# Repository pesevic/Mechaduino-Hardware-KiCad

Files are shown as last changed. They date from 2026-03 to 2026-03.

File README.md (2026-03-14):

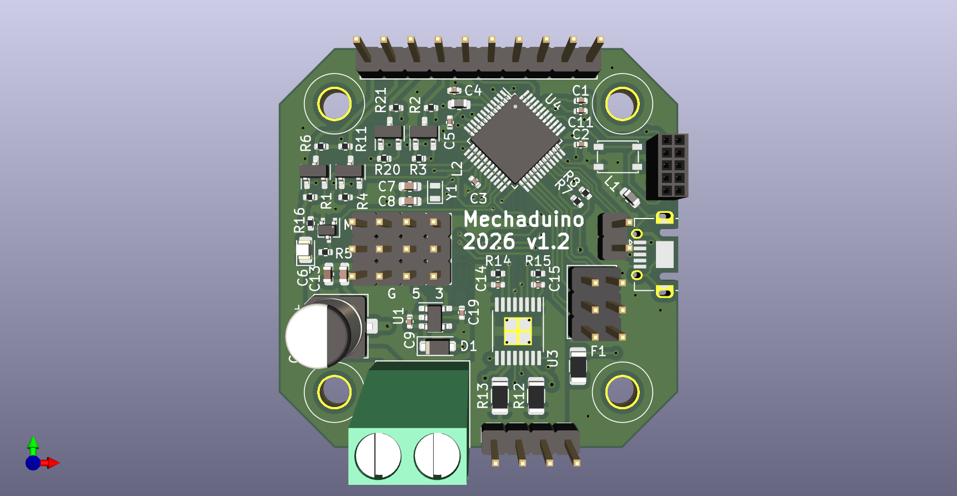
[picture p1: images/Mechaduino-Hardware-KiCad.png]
3D Render of Mechaduino PCB

# Overview
This repository contains an updated KiCad port of [jcchurch13's](https://github.com/jcchurch13/Mechaduino-Hardware) Mechaduino hardware. 

As a part of my master's thesis, I wanted to revive the Mechaduino-based [TorqueTuner](https://github.com/IDMIL/TorqueTuner), a rotary haptic device developed at the Input Devices and Music Interaction Laboratory (IDMIL) at McGill University. Since the Mechaduino has been out of production for some years, and because the original design files are in EAGLE (a now-defunct, proprietary software), I have ported the schematics and board layout to KiCad, a free and open-source (and incredibly powerful) PCB design software. 

While retaining the original circuit design, I have updated the schematics and created a new PCB layout from scratch, using KiCad's built-in component libraries. I have also included PCB fabrication/assembly files (.gbr, .drl, BOM, CPL). Most importantly, since the design is now more readily accessible, I hope it will be much easier to adapt and redesign the hardware for various stepper motors and applications.

Below, I have included some useful information if you wish to adopt or adapt the Mechaduino for your own project.

# Guide
This section serves as a guide for manufacturing and programming the Mechaduino.
## Mechaduino Summary
The [Mechaduino](https://github.com/jcchurch13/Mechaduino-Hardware) is an open-source stepper motor servo designed by [Tropical Labs](https://tropical-labs.com/mechaduino/). Its relatively small size and affordability make it attractive for mechatronics applications.

Integrated circuits on the board include a motor driver (A4954), magnetic encoder (AS5047D), 3.3 V linear voltage regulator (TLV70233), and an Arduino Zero-compatible microcontroller (ATSAMD21G18A-A). It can be powered via USB or an external 5 V source. The motor is powered through a terminal block, accepting a supply voltage between 8 V and 35 V. A range of Arduino I/O pins are accessible through the header pins, including those for I2C and SPI communication. See the schematic for more detail.

The board is designed to fit onto the back of a NEMA 17 motor.

## PCB Manufacturing
If you wish to obtain Mechaduino PCBs for yourself, you may follow what I suggest below, which is how I ordered them for myself.

For manufacturing and assembly, I used [jlcpcb.com](jlcpcb.com). Upload the zipped fabrication files to JLC, and add the PCB assembly option. Since two-layer boards can only be assembled on one side, choose the top side. The magnetic encoder and its decoupling capacitor can be soldered manually later. Upload the corresponding bill of materials and component position list .csv files. **Note that you may need to select alternative parts or reposition components in the board preview.** I have had to flip C12 and align J9 (USB connector) each time I've processed the PCBs.

## Device Assembly
Besides the Mechaduino PCB, you will need the following parts (the links direct to the parts I used):
 - [a NEMA 17 stepper motor](https://www.omc-stepperonline.com/nema-17-bipolar-45ncm-64oz-in-2a-42x42x40mm-4-wires-w-1m-cable-connector-17hs16-2004s1),
 - [a diametrically magnetized NdFeB magnet](https://www.digikey.ca/en/products/detail/radial-magnets-inc/8996/5126078),
 - an AS5074D magnetic encoder IC,
 - an 0.1 uF 0805 SMD capacitor,
 - 2.54 mm pitch header pins,
 - long M3 screws/threaded rods,
 - standoffs of some sort (I used washers), and
 - super glue.

Follow these steps (based on instructions in [Tropical Labs' manual](https://tropical-labs.com/wp-content/uploads/2018/11/Mechaduino-Manual-0.1.3.pdf)):
1. Solder the encoder and capacitor to the back of the PCB with an iron/reflow/oven. Also add the header pins.
2. Super glue the magnet onto the back of the motor shaft. Center it as much as possible.
3. Mount the PCB to the motor using the threaded rods and standoffs. The PCB should sit a couple of milimeters away from the motor.

Your Mechaduino should now be ready to be programmed.

## Programming
Flashing an Arduino Zero bootloader onto the custom MCU circuit was, for me, the most challenging part of this build. I used an ST-LINK V2 USB programmer paired with [Adafruit Adalink](https://github.com/adafruit/Adafruit_Adalink) to upload the bootloader via the PCB's SWD pins. This may be easier on Mac, but I can only speak for the Herculean procedure required for Windows users. Besides the USB programmer, you will need some way of connecting the programmer to the pins. I used an SWD breakout board connected to the programmer with jumper wires.

Follow the installation instructions on the [Adalink repository](https://github.com/adafruit/Adafruit_Adalink). Note, however, that I could not get Adalink to work with any version of Python newer than 2.7.13 (this was using Adalink 2.2.0 and OpenOCD 0.12.0). You may need to downgrade Python to an older version.

Once you have confirmed that Adalink is working in CMD, clone the [ArduinoCore-samd repository](https://github.com/arduino/arduinocore-samd) to get the bootloader. CD into `/ArduinoCore-samd/bootloaders/zero`. Wipe the board and flash the bootloader with the following two commands:
```
adalink atsamd21g18 -p stlink -w
adalink -v atsamd21g18 -p stlink -h samd21_sam_ba.hex
```
Check whether the 5888 bytes are verified. If not, unplugging and plugging the ST-LINK USB dongle into my computer seemed to fix things. Once the MCU has successfully been flashed, connect the Mechaduino to your computer via the micro-USB port. Double-pressing the reset button on the PCB should make the device appear as an Arduino Zero in Device Manager or in the Arduino IDE.

Finally, clone the [Mechaduino Firmware](https://github.com/jcchurch13/Mechaduino-Firmware) repository and upload the code to the board via the Arduino IDE. You should now have a fully functioning Mechaduino. Run the calibration routine and tests as described in [Tropical Labs' manual](https://tropical-labs.com/wp-content/uploads/2018/11/Mechaduino-Manual-0.1.3.pdf).

# License
This project is released under the [Creative Commons Attribution-ShareAlike 4.0](https://creativecommons.org/licenses/by-sa/4.0/) license, and is not endorsed by the original creator.

*No generative AI was used in any part of this project.*

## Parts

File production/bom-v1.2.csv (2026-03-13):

Designator | Footprint | Quantity | Value | LCSC Part #
C1, C14, C15, C16, C2, C3, C4, C5 | 402 | 8 | 0.1u | C169842
C11, C19, C9 | 402 | 3 | 1.0u | C29266
C12 | CP_Elec_6.3x7.7 | 1 | 100u | C178560
C13 | 603 | 1 | 1.0u | C5673
C6 | 603 | 1 | 0.01u | C1589
C7, C8 | 603 | 2 | 18p | C165734
D1 | D_SOD-123F | 1 | SMF5.0CA | C283867
F1 | 1206 | 1 | ASMD1206-050 | C883127
J1 | TerminalBlock_Phoenix_MKDS-1,5-2_1x02_P5.00mm_Horizontal | 1 | Screw_Terminal_01x02 | C3817933
J9 | USB_Micro-AB_Molex_47590-0001 | 1 | USB_B_Micro | C136001
L1, L2 | 603 | 2 | BLM18PG471SN1D | C97853
LED1 | 805 | 1 | Green | C2899888
Q1, Q2, Q3, Q4 | SOT-23-3 | 4 | BSS138 | C534601
Q5 | SOT-323_SC-70 | 1 | 2N7002 | C139444
R1, R11, R2, R20, R21, R3, R4, R6 | 402 | 8 | 10k | C71617
R12, R13 | 1206 | 2 | 0.15 | C37936
R14, R15 | 402 | 2 | 1k | C71623
R16 | 402 | 1 | 100k | C481918
R5 | 402 | 1 | 330 | C25104
R7, R8 | 402 | 2 | 4.7k | C482193
SW1 | SW_SPST_PTS810 | 1 | SW_SPST | C221896
U1 | SOT-23-5 | 1 | TLV70233_SOT23-5 | C110287
U2 | TSSOP-14_4.4x5mm_P0.65mm | 1 | AS5047D | C2693743
U3 | TSSOP-16-1EP_4.4x5mm_P0.65mm_EP3x3mm_ThermalVias | 1 | A4954 | C2688265
U4 | TQFP-48_7x7mm_P0.5mm | 1 | ATSAMD21G18A-A | C78624
Y1 | Crystal_SMD_2012-2Pin_2.0x1.2mm | 1 | 32.768k | C907552

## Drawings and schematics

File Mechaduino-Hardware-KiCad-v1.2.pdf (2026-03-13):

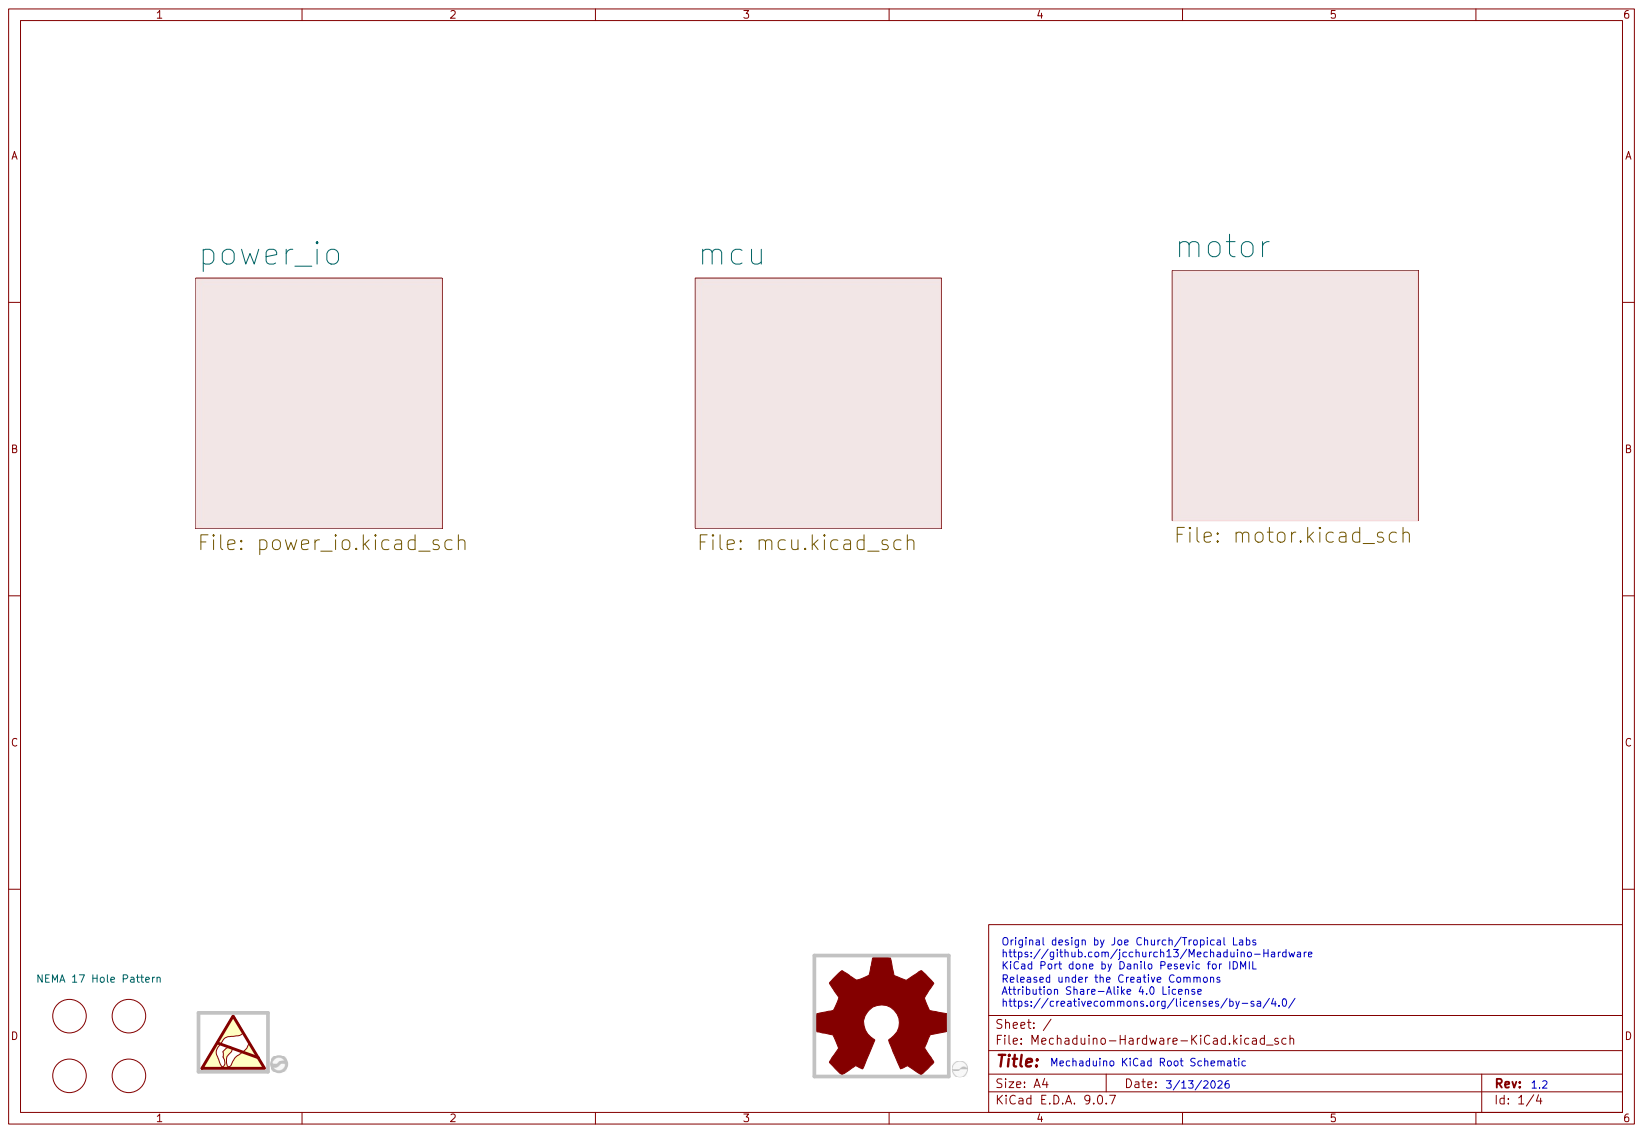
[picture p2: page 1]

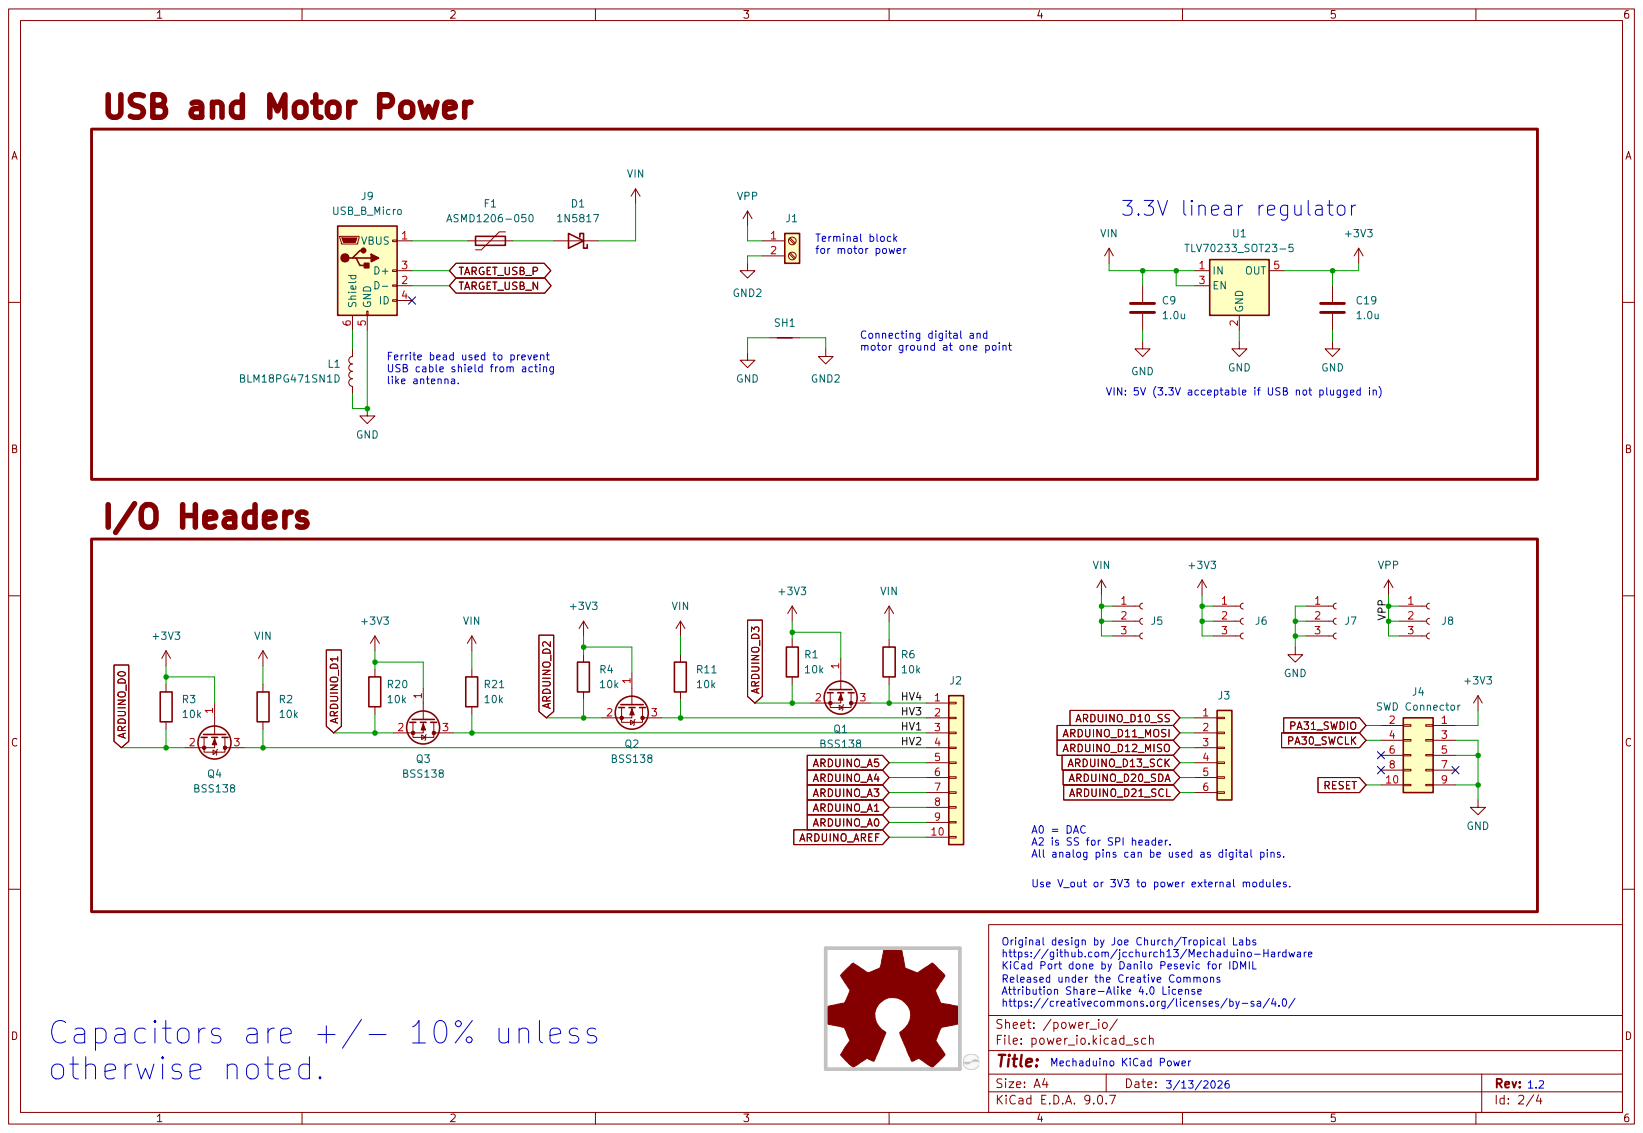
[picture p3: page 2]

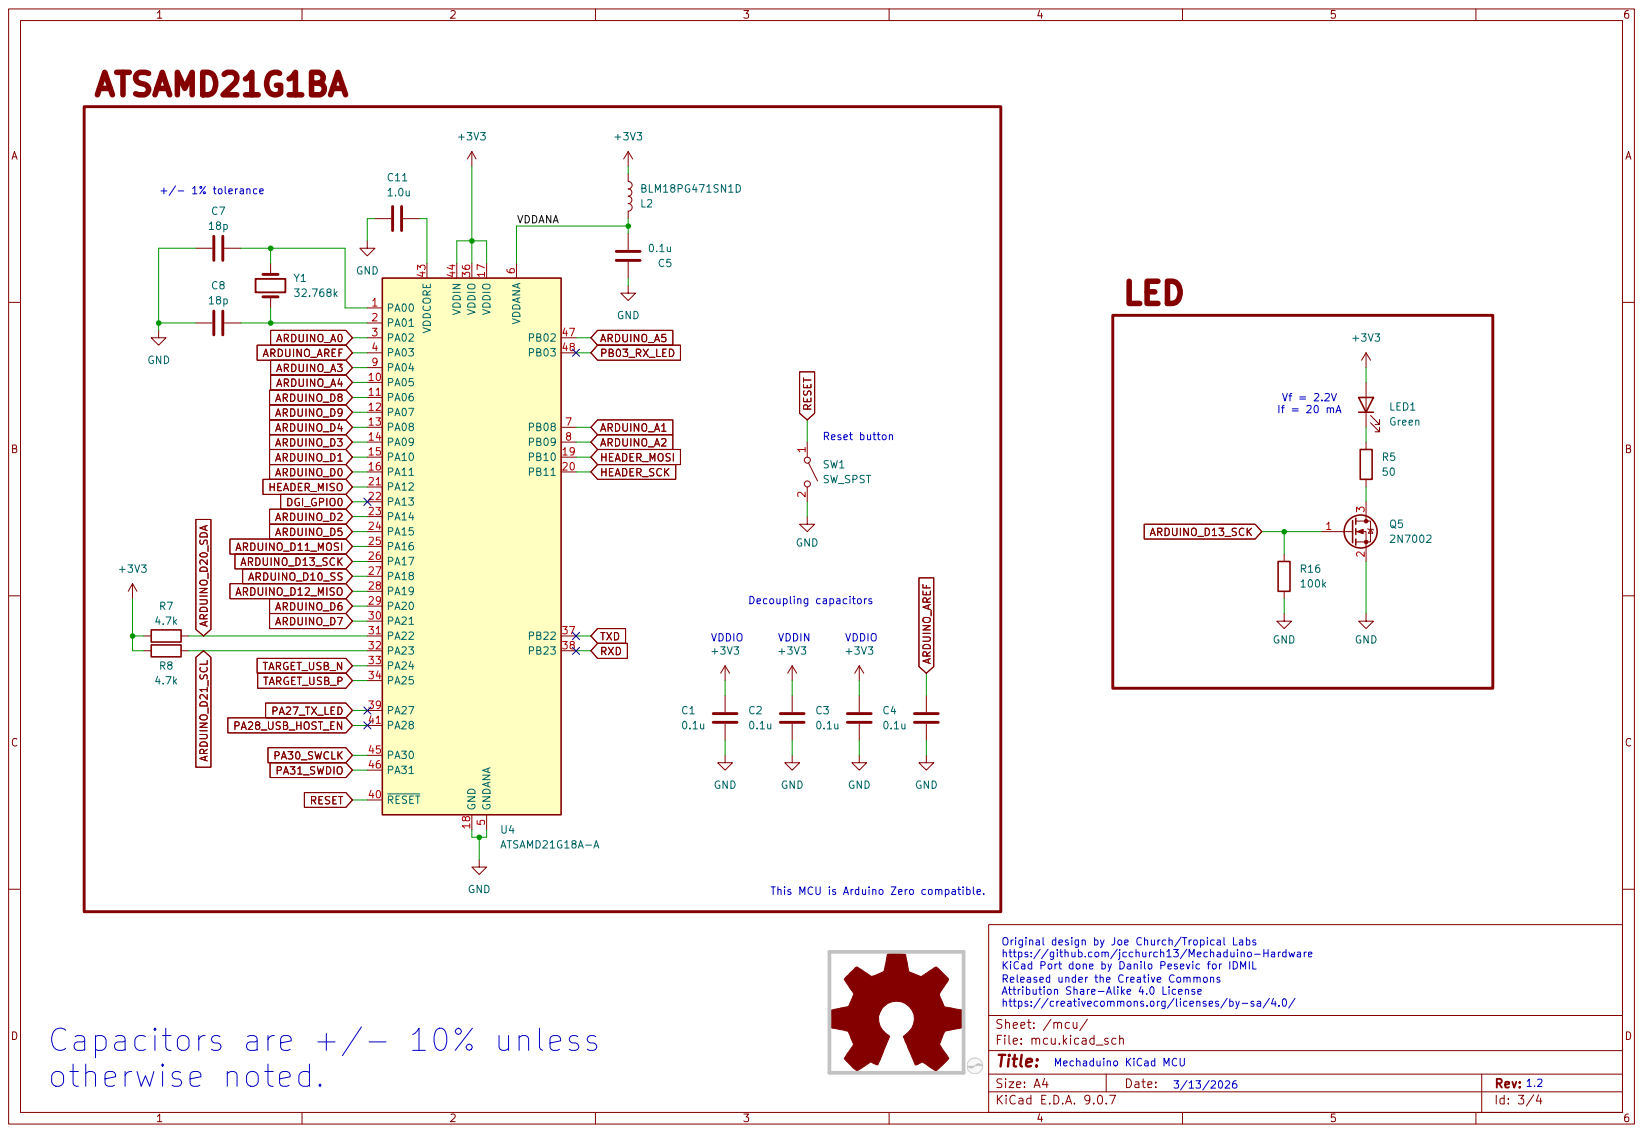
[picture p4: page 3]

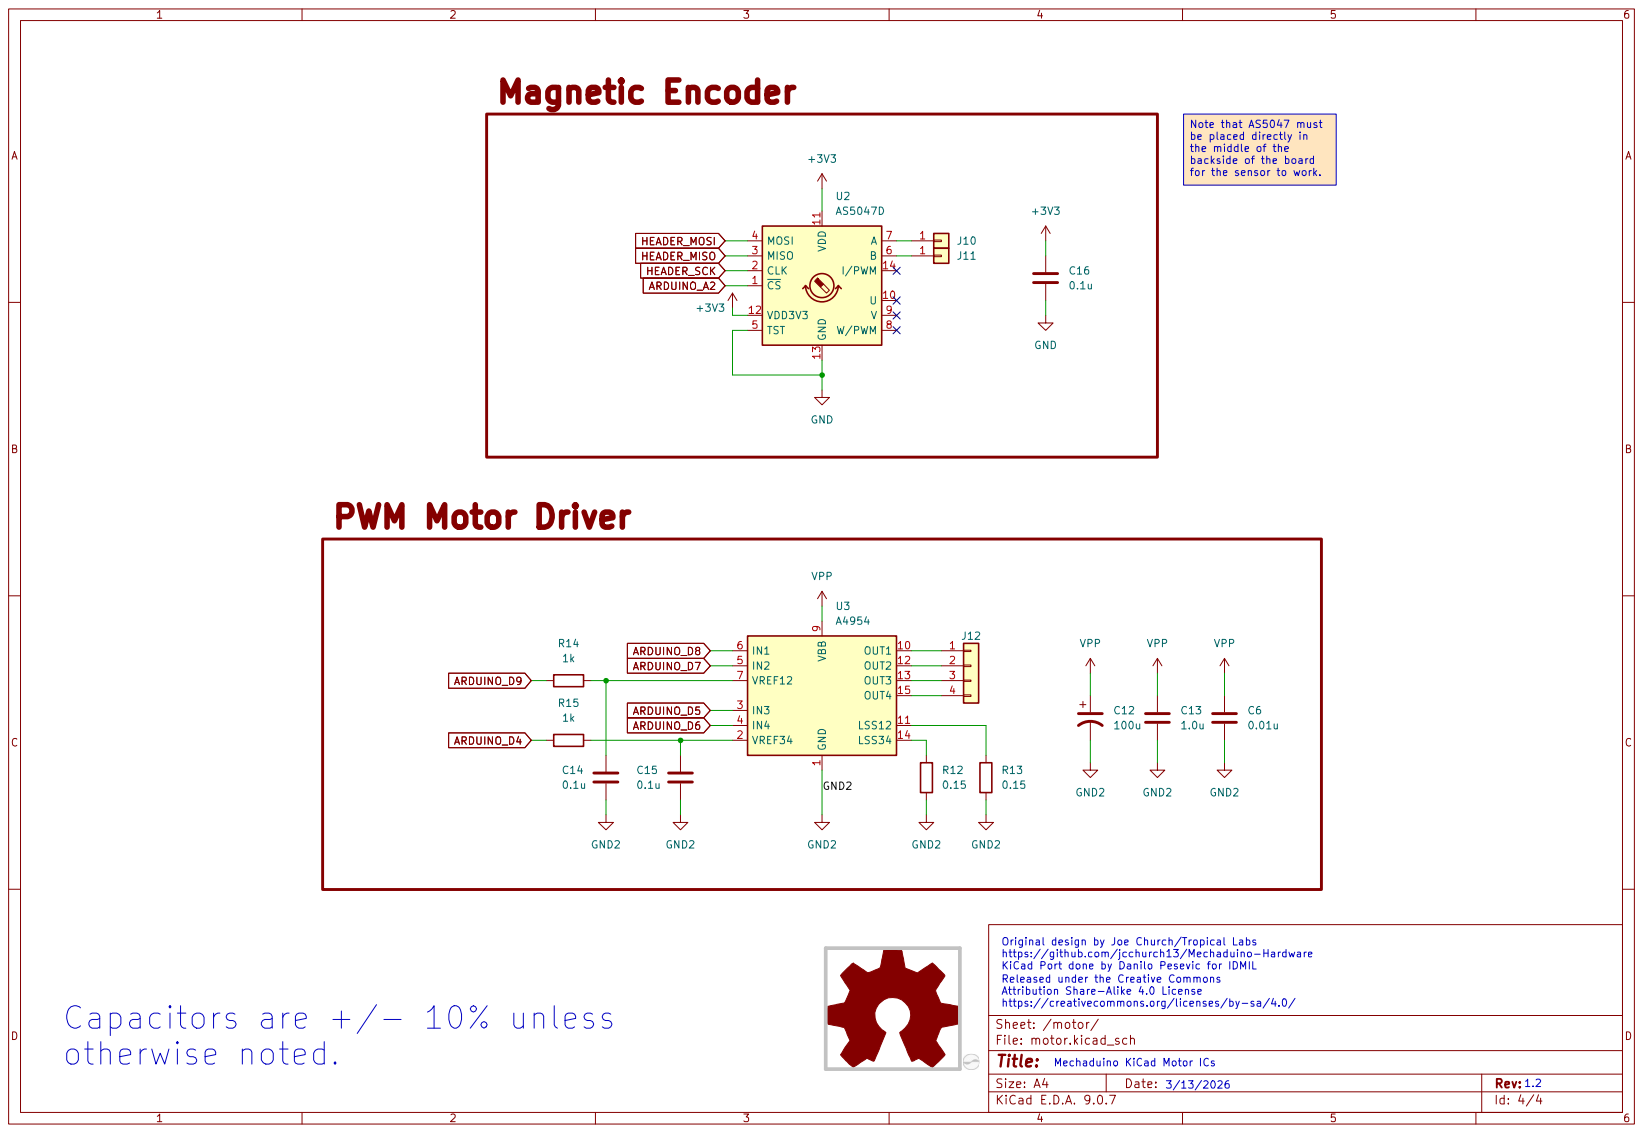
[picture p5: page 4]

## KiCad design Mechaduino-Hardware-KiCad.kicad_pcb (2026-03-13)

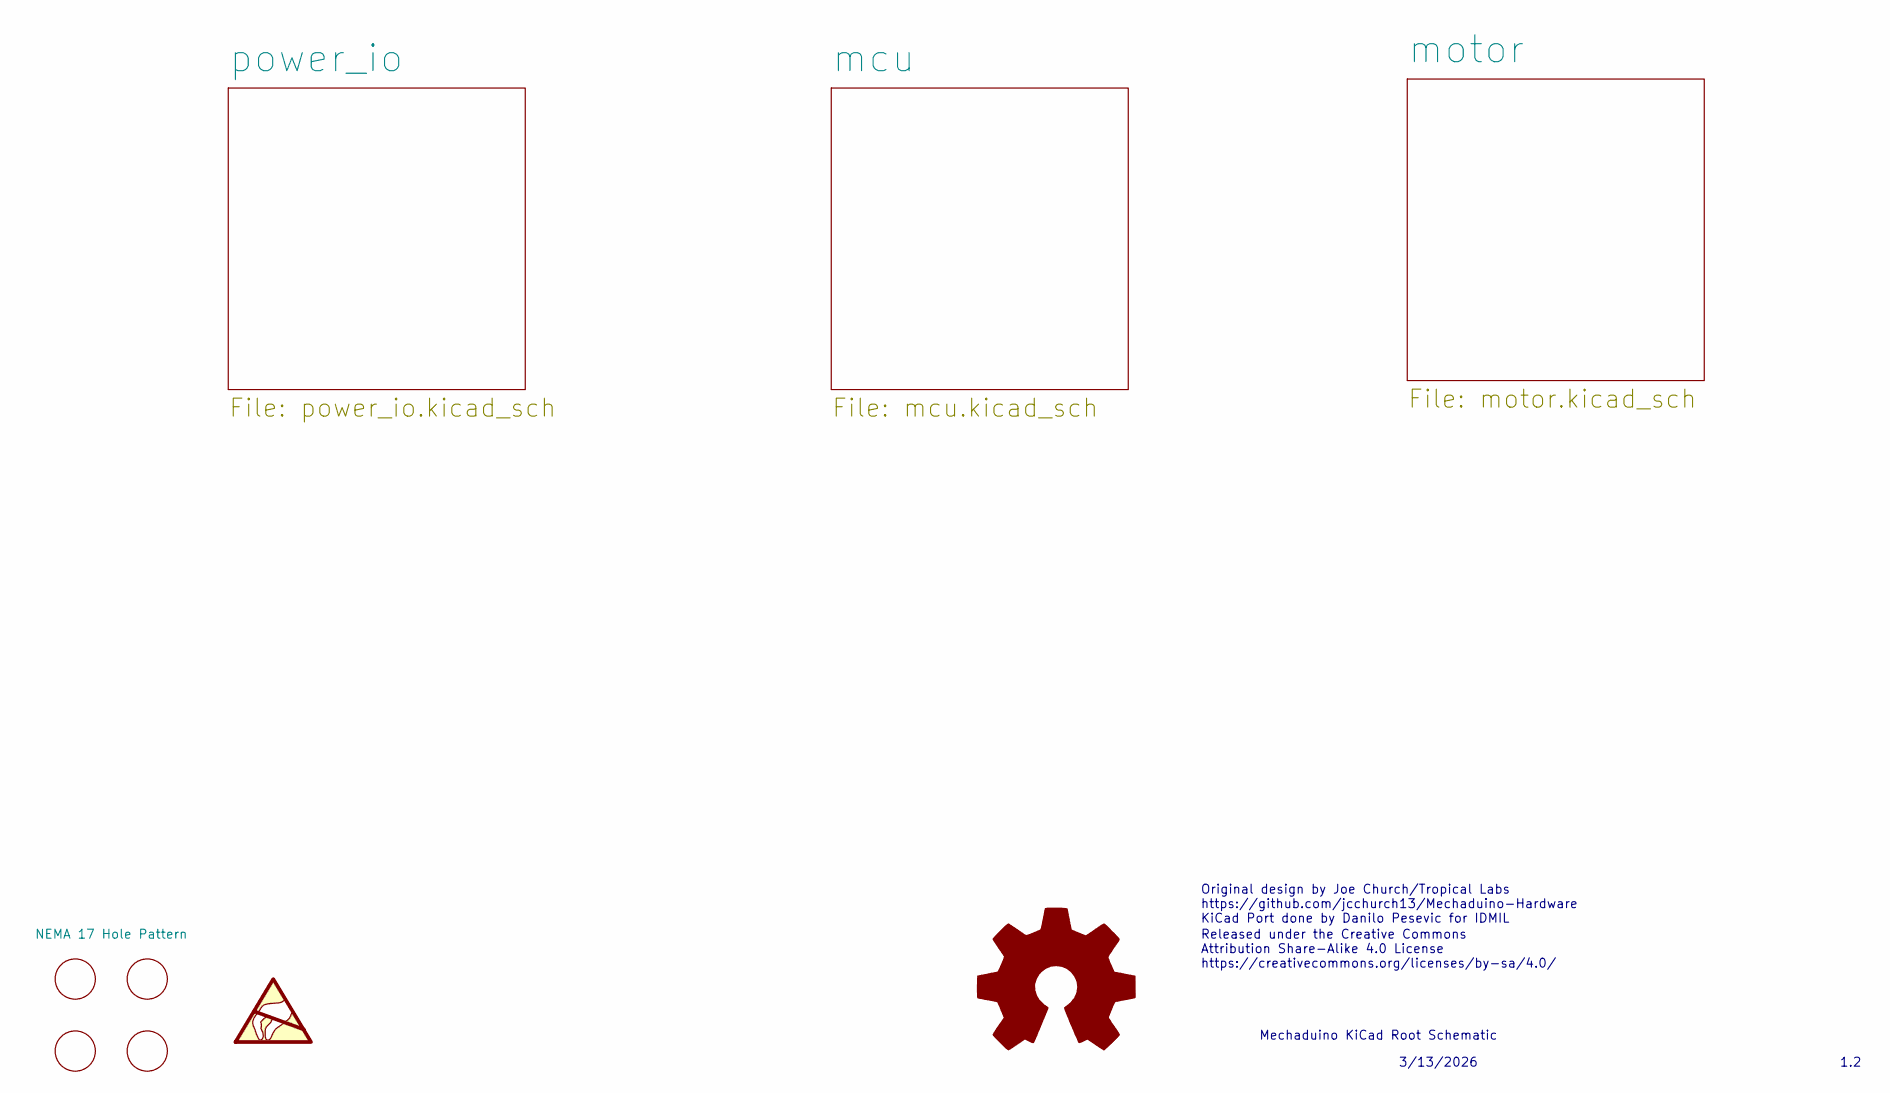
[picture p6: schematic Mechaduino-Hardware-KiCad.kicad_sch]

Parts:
J13: NEMA 17 Hole Pattern

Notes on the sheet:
Mechaduino KiCad Root Schematic
Original design by Joe Church/Tropical Labs https://github.com/jcchurch13/Mechaduino-Hardware KiCad Port done by Danilo Pesevic for IDMIL
3/13/2026
Released under the Creative Commons Attribution Share-Alike 4.0 License https://creativecommons.org/licenses/by-sa/4.0/
1.2

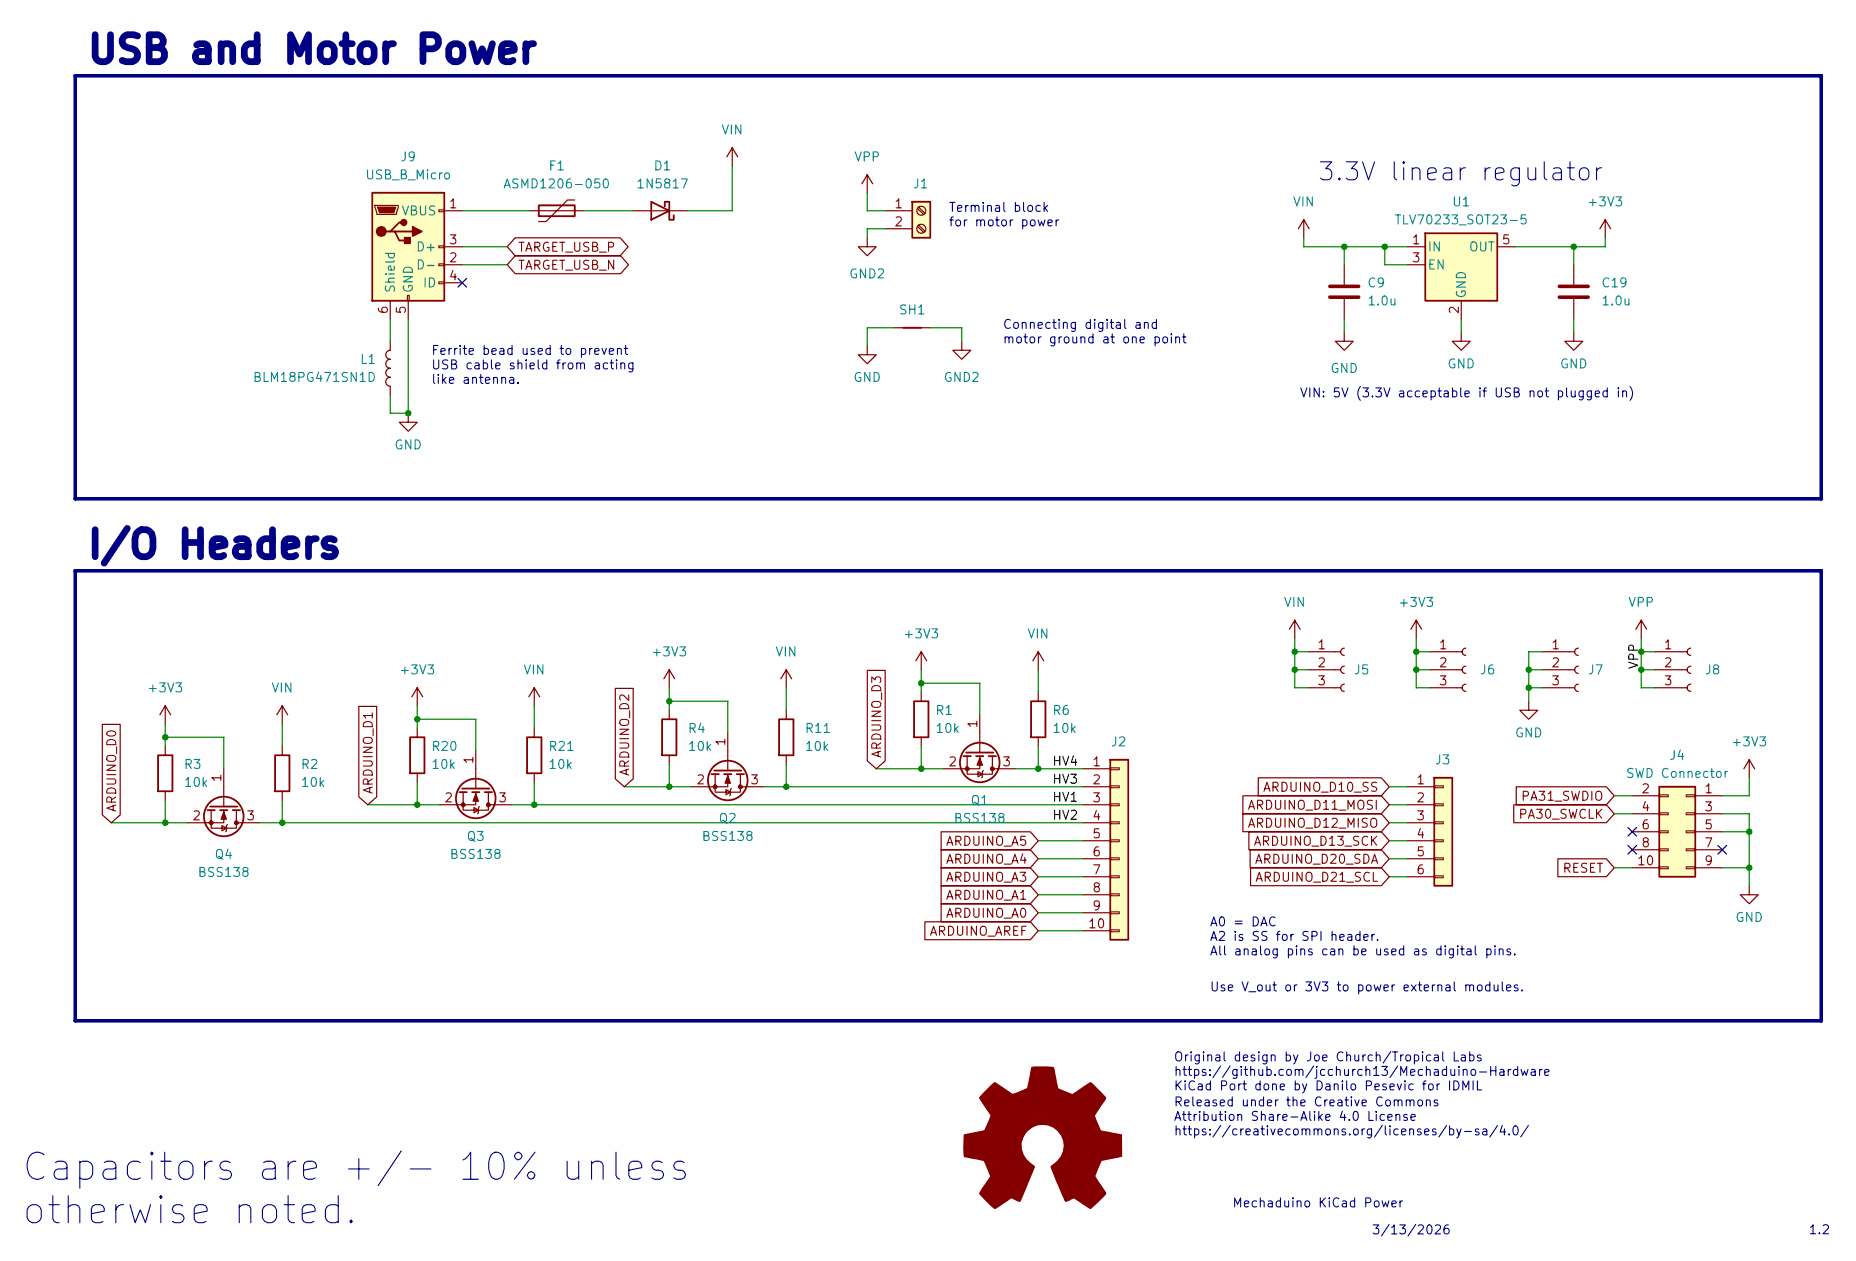
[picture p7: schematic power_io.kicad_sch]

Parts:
C9, C19: 1.0u; C_0402_1005Metric
D1: 1N5817; D_SOD-123F
F1: ASMD1206-050; Fuse_1206_3216Metric
J1: Screw_Terminal_01x02; TerminalBlock_Phoenix_MKDS-1,5-2_1x02_P5.00mm_Horizontal
J2: Conn_01x10; PinHeader_1x10_P2.54mm_Vertical
J3: Conn_01x06; PinHeader_2x03_P2.54mm_Vertical
J4: SWD Connector; PinSocket_2x05_P1.27mm_Vertical
J5, J6, J7, J8: Conn_01x03_Socket; PinHeader_1x03_P2.54mm_Vertical
J9: USB_B_Micro; USB_Micro-AB_Molex_47590-0001
L1: BLM18PG471SN1D; L_0603_1608Metric
Q1, Q2, Q3, Q4: BSS138; SOT-23-3
R1, R2, R3, R4, R6, R11, R20, R21: 10k; R_0402_1005Metric
SH1: NetTie_2; NetTie-2_THT_Pad1.0mm
U1: TLV70233_SOT23-5; SOT-23-5

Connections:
+3V3: C19.1, J4.1, J6.1, J6.2, J6.3, Q1.1 (G), Q2.1 (G), Q3.1 (G), Q4.1 (G), R1.1, R3.1, R4.1, R20.1, U1.5 (OUT); also elsewhere on the board
/power_io/HV1: J2.3, Q3.3 (D), R21.2
/power_io/HV2: J2.4, Q4.3 (D), R2.2
/power_io/HV3: J2.2, Q2.3 (D), R11.2
/power_io/HV4: J2.1, Q1.3 (D), R6.2
ARDUINO_A0: J2.9; also elsewhere on the board
ARDUINO_A1: J2.8; also elsewhere on the board
ARDUINO_A3: J2.7; also elsewhere on the board
ARDUINO_A4: J2.6; also elsewhere on the board
ARDUINO_A5: J2.5; also elsewhere on the board
ARDUINO_AREF: J2.10; also elsewhere on the board
ARDUINO_D0: Q4.2 (S), R3.2; also elsewhere on the board
ARDUINO_D1: Q3.2 (S), R20.2; also elsewhere on the board
ARDUINO_D2: Q2.2 (S), R4.2; also elsewhere on the board
ARDUINO_D3: Q1.2 (S), R1.2; also elsewhere on the board
ARDUINO_D10_SS: J3.1; also elsewhere on the board
ARDUINO_D11_MOSI: J3.2; also elsewhere on the board
ARDUINO_D12_MISO: J3.3; also elsewhere on the board
ARDUINO_D13_SCK: J3.4; also elsewhere on the board
ARDUINO_D20_SDA: J3.5; also elsewhere on the board
ARDUINO_D21_SCL: J3.6; also elsewhere on the board
GND: C9.2, C19.2, J4.3, J4.5, J4.9, J7.1, J7.2, J7.3, J9.5 (GND), L1.1, SH1.1, U1.2 (GND); also elsewhere on the board
GND2: J1.2, SH1.2; also elsewhere on the board
unnamed: D1.2 (A), F1.2
unnamed: J9.6 (Shield), L1.2
unnamed: F1.1, J9.1 (VBUS)
PA30_SWCLK: J4.4; also elsewhere on the board
PA31_SWDIO: J4.2; also elsewhere on the board
RESET: J4.10; also elsewhere on the board
TARGET_USB_N: J9.2 (D-); also elsewhere on the board
TARGET_USB_P: J9.3 (D+); also elsewhere on the board
VIN: C9.1, D1.1 (K), J5.1, J5.2, J5.3, R2.1, R6.1, R11.1, R21.1, U1.1 (IN), U1.3 (EN)
VPP: J1.1, J8.1, J8.2, J8.3; also elsewhere on the board

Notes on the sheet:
1.2
3.3V linear regulator
Use V_out or 3V3 to power external modules.
Mechaduino KiCad Power
Ferrite bead used to prevent USB cable shield from acting like antenna.
VIN: 5V (3.3V acceptable if USB not plugged in)
3/13/2026
Original design by Joe Church/Tropical Labs https://github.com/jcchurch13/Mechaduino-Hardware KiCad Port done by Danilo Pesevic for IDMIL
Connecting digital and motor ground at one point
Capacitors are +/- 10% unless otherwise noted.
Terminal block for motor power
I/O Headers
Released under the Creative Commons Attribution Share-Alike 4.0 License https://creativecommons.org/licenses/by-sa/4.0/
USB and Motor Power
A0 = DAC A2 is SS for SPI header. All analog pins can be used as digital pins.

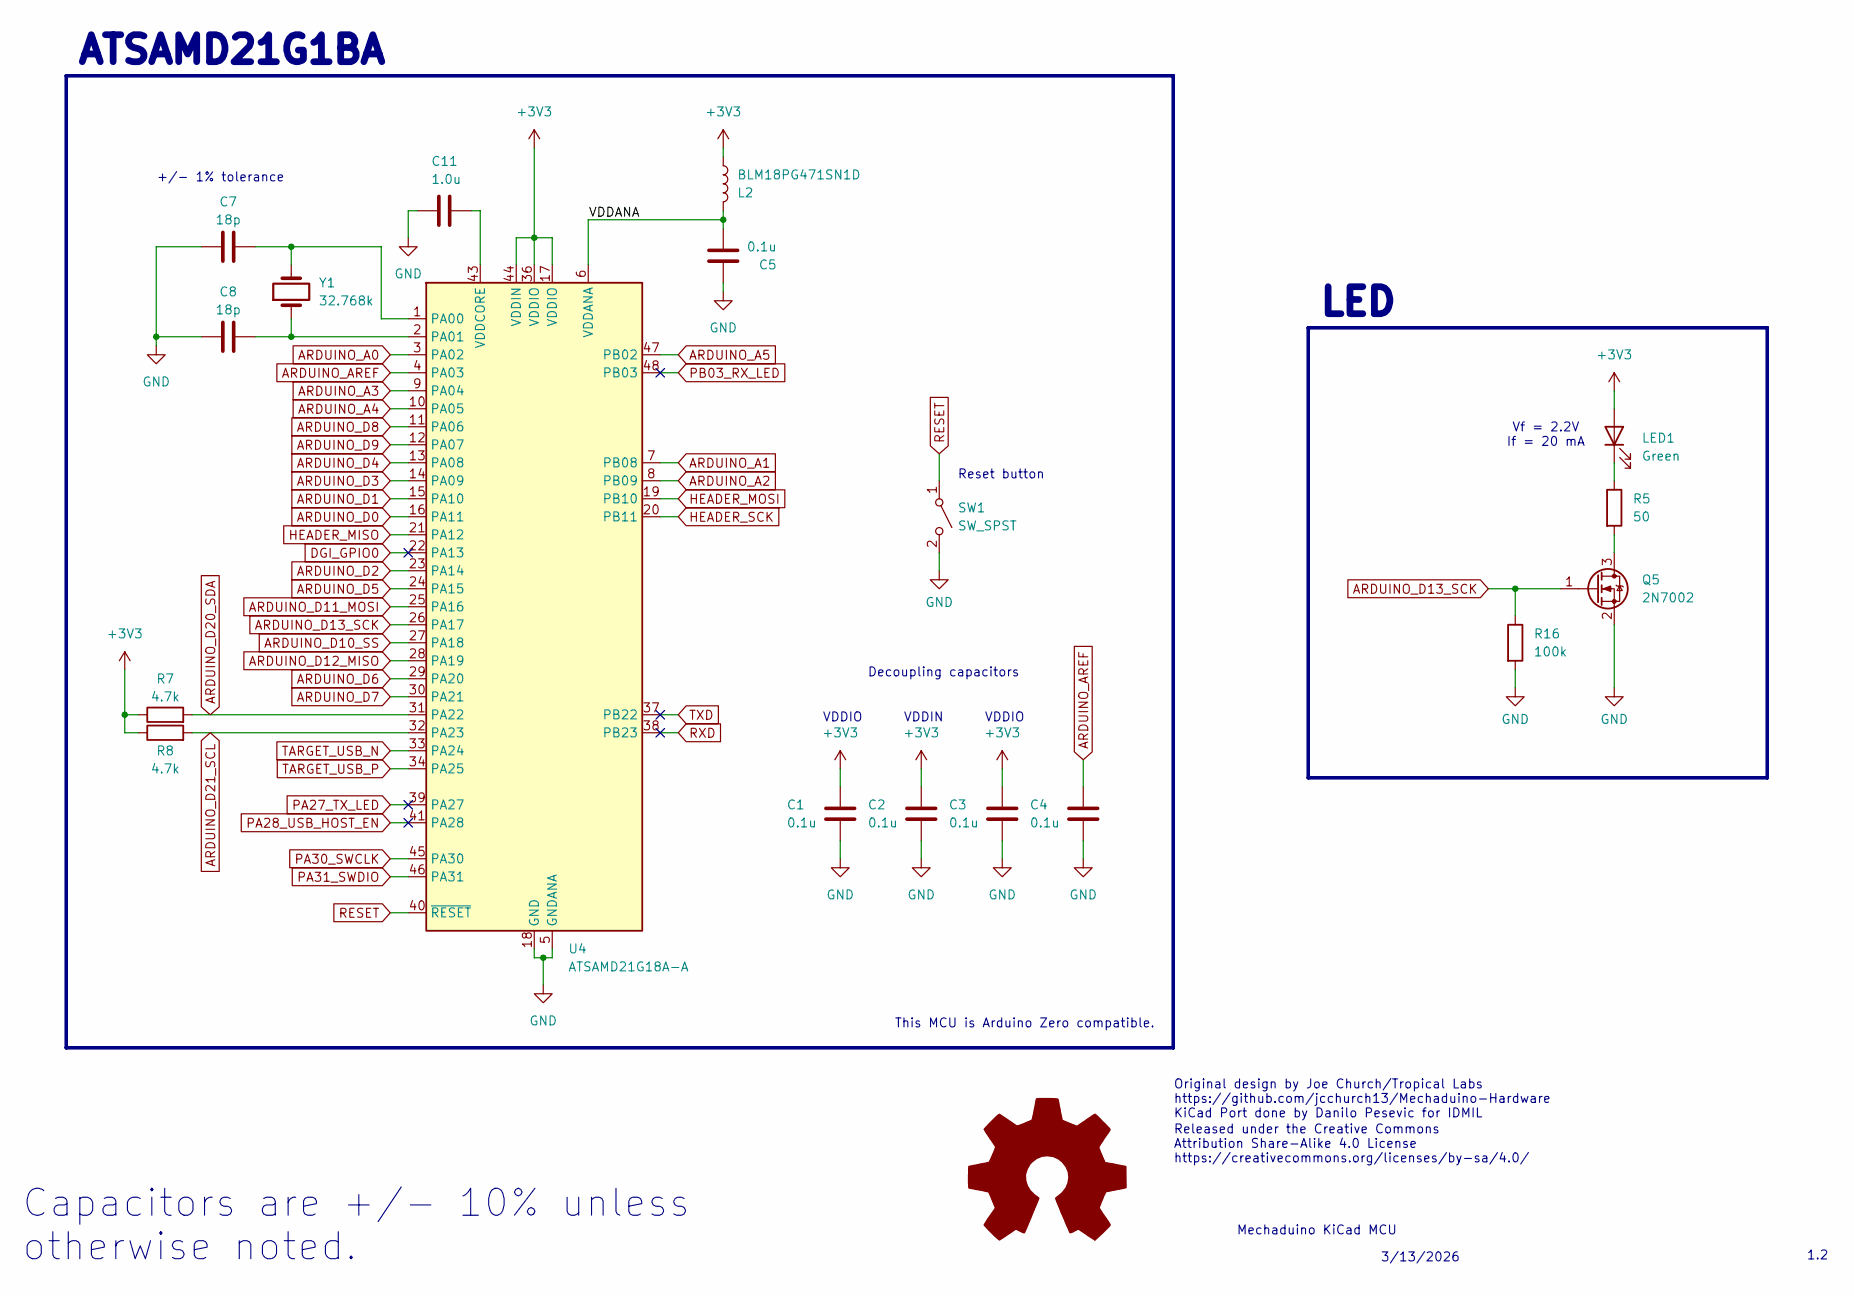
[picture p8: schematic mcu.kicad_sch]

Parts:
C1, C2, C3, C4, C5: 0.1u; C_0402_1005Metric
C7, C8: 18p; C_0603_1608Metric
C11: 1.0u; C_0402_1005Metric
L2: BLM18PG471SN1D; L_0603_1608Metric
LED1: Green; LED_0805_2012Metric
Q5: 2N7002; SOT-323_SC-70
R5: 50; R_0402_1005Metric
R7, R8: 4.7k; R_0402_1005Metric
R16: 100k; R_0402_1005Metric
SW1: SW_SPST; SW_SPST_PTS810
U4: ATSAMD21G18A-A; TQFP-48_7x7mm_P0.5mm
Y1: 32.768k; Crystal_SMD_2012-2Pin_2.0x1.2mm

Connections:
+3V3: C1.1, C2.1, C3.1, L2.1, LED1.2 (A), R7.1, R8.1, U4.17 (VDDIO), U4.36 (VDDIO), U4.44 (VDDIN); also elsewhere on the board
/mcu/VDDANA: C5.2, L2.2, U4.6 (VDDANA)
ARDUINO_A0: U4.3 (PA02); also elsewhere on the board
ARDUINO_A1: U4.7 (PB08); also elsewhere on the board
ARDUINO_A2: U4.8 (PB09); also elsewhere on the board
ARDUINO_A3: U4.9 (PA04); also elsewhere on the board
ARDUINO_A4: U4.10 (PA05); also elsewhere on the board
ARDUINO_A5: U4.47 (PB02); also elsewhere on the board
ARDUINO_AREF: C4.1, U4.4 (PA03); also elsewhere on the board
ARDUINO_D0: U4.16 (PA11); also elsewhere on the board
ARDUINO_D1: U4.15 (PA10); also elsewhere on the board
ARDUINO_D2: U4.23 (PA14); also elsewhere on the board
ARDUINO_D3: U4.14 (PA09); also elsewhere on the board
ARDUINO_D4: U4.13 (PA08); also elsewhere on the board
ARDUINO_D5: U4.24 (PA15); also elsewhere on the board
ARDUINO_D6: U4.29 (PA20); also elsewhere on the board
ARDUINO_D7: U4.30 (PA21); also elsewhere on the board
ARDUINO_D8: U4.11 (PA06); also elsewhere on the board
ARDUINO_D9: U4.12 (PA07); also elsewhere on the board
ARDUINO_D10_SS: U4.27 (PA18); also elsewhere on the board
ARDUINO_D11_MOSI: U4.25 (PA16); also elsewhere on the board
ARDUINO_D12_MISO: U4.28 (PA19); also elsewhere on the board
ARDUINO_D13_SCK: Q5.1 (G), R16.1, U4.26 (PA17); also elsewhere on the board
ARDUINO_D20_SDA: R7.2, U4.31 (PA22); also elsewhere on the board
ARDUINO_D21_SCL: R8.2, U4.32 (PA23); also elsewhere on the board
DGI_GPIO0: U4.22 (PA13)
GND: C1.2, C2.2, C3.2, C4.2, C5.1, C7.1, C8.1, C11.2, Q5.2 (S), R16.2, SW1.2 (B), U4.5 (GNDANA), U4.18 (GND), U4.35 (GND), U4.42 (GND); also elsewhere on the board
HEADER_MISO: U4.21 (PA12); also elsewhere on the board
HEADER_MOSI: U4.19 (PB10); also elsewhere on the board
HEADER_SCK: U4.20 (PB11); also elsewhere on the board
unnamed: LED1.1 (K), R5.1
unnamed: Q5.3 (D), R5.2
unnamed: C7.2, U4.1 (PA00), Y1.2
unnamed: C8.2, U4.2 (PA01), Y1.1
unnamed: C11.1, U4.43 (VDDCORE)
PA27_TX_LED: U4.39 (PA27)
PA28_USB_HOST_EN: U4.41 (PA28)
PA30_SWCLK: U4.45 (PA30); also elsewhere on the board
PA31_SWDIO: U4.46 (PA31); also elsewhere on the board
PB03_RX_LED: U4.48 (PB03)
RESET: SW1.1 (A), U4.40 (~RESET); also elsewhere on the board
RXD: U4.38 (PB23)
TARGET_USB_N: U4.33 (PA24); also elsewhere on the board
TARGET_USB_P: U4.34 (PA25); also elsewhere on the board
TXD: U4.37 (PB22)

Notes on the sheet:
VDDIO
Reset button
Capacitors are +/- 10% unless otherwise noted.
LED
VDDIN
Released under the Creative Commons Attribution Share-Alike 4.0 License https://creativecommons.org/licenses/by-sa/4.0/
Original design by Joe Church/Tropical Labs https://github.com/jcchurch13/Mechaduino-Hardware KiCad Port done by Danilo Pesevic for IDMIL
ATSAMD21G1BA
+/- 1% tolerance
Vf = 2.2V If = 20 mA
Decoupling capacitors
Mechaduino KiCad MCU
This MCU is Arduino Zero compatible.
1.2
3/13/2026

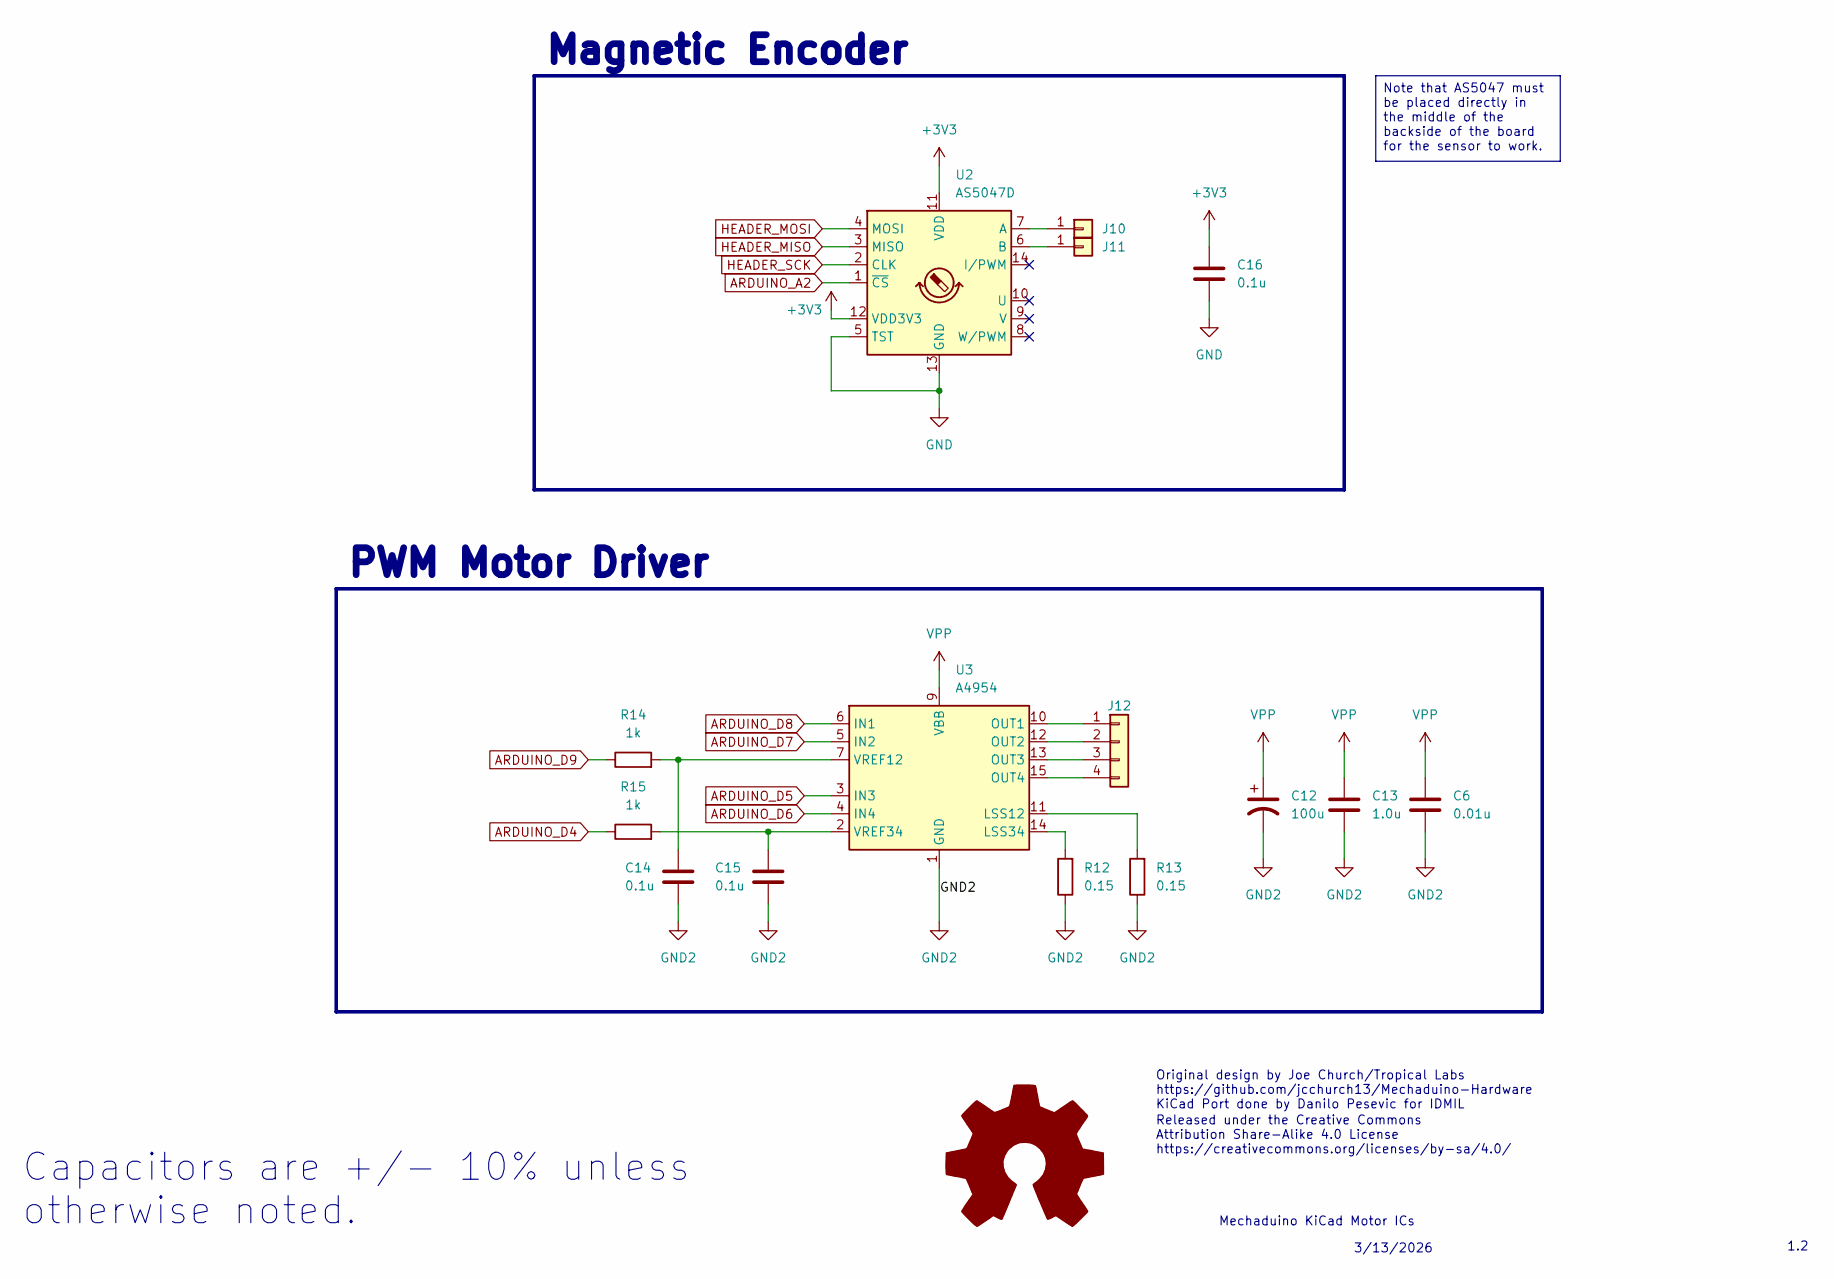
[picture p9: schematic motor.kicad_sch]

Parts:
C6: 0.01u; C_0603_1608Metric
C12: 100u; CP_Elec_6.3x7.7
C13: 1.0u; C_0603_1608Metric
C14, C15: 0.1u; C_0402_1005Metric
C16: 0.1u; C_0805_2012Metric_Pad1.18x1.45mm_HandSolder
J10, J11: Conn_01x01; PinHeader_1x01_P2.54mm_Vertical
J12: Conn_01x04; PinHeader_1x04_P2.54mm_Vertical
R12, R13: 0.15; R_1206_3216Metric
R14, R15: 1k; R_0402_1005Metric
U2: AS5047D; TSSOP-14_4.4x5mm_P0.65mm
U3: A4954; TSSOP-16-1EP_4.4x5mm_P0.65mm_EP3x3mm_ThermalVias

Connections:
+3V3: C16.1, U2.11 (VDD), U2.12 (VDD3V3); also elsewhere on the board
ARDUINO_A2: U2.1 (~CS); also elsewhere on the board
ARDUINO_D4: R15.1; also elsewhere on the board
ARDUINO_D5: U3.3 (IN3); also elsewhere on the board
ARDUINO_D6: U3.4 (IN4); also elsewhere on the board
ARDUINO_D7: U3.5 (IN2); also elsewhere on the board
ARDUINO_D8: U3.6 (IN1); also elsewhere on the board
ARDUINO_D9: R14.1; also elsewhere on the board
GND: C16.2, U2.5 (TST), U2.13 (GND); also elsewhere on the board
GND2: C6.2, C12.2, C13.2, C14.2, C15.2, R12.1, R13.1, U3.1 (GND), U3.8 (GND), U3.17 (GND); also elsewhere on the board
HEADER_MISO: U2.3 (MISO); also elsewhere on the board
HEADER_MOSI: U2.4 (MOSI); also elsewhere on the board
HEADER_SCK: U2.2 (CLK); also elsewhere on the board
unnamed: J10.1, U2.7 (A)
unnamed: J11.1, U2.6 (B)
unnamed: J12.1, U3.10 (OUT1)
unnamed: J12.2, U3.12 (OUT2)
unnamed: J12.3, U3.13 (OUT3)
unnamed: J12.4, U3.15 (OUT4)
unnamed: R13.2, U3.11 (LSS12)
unnamed: R12.2, U3.14 (LSS34)
unnamed: C14.1, R14.2, U3.7 (VREF12)
unnamed: C15.1, R15.2, U3.2 (VREF34)
VPP: C6.1, C12.1, C13.1, U3.9 (VBB), U3.16 (VBB); also elsewhere on the board

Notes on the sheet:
3/13/2026
Original design by Joe Church/Tropical Labs https://github.com/jcchurch13/Mechaduino-Hardware KiCad Port done by Danilo Pesevic for IDMIL
Released under the Creative Commons Attribution Share-Alike 4.0 License https://creativecommons.org/licenses/by-sa/4.0/
1.2
Mechaduino KiCad Motor ICs
Magnetic Encoder
Capacitors are +/- 10% unless otherwise noted.
PWM Motor Driver
Note that AS5047 must be placed directly in the middle of the backside of the board for the sensor to work.

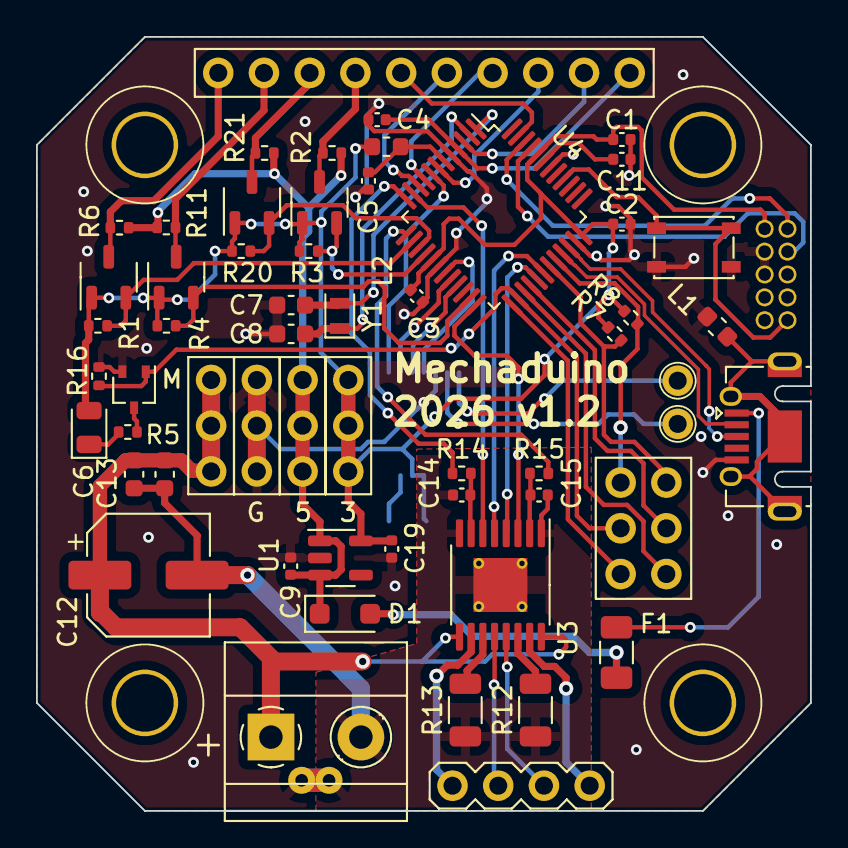
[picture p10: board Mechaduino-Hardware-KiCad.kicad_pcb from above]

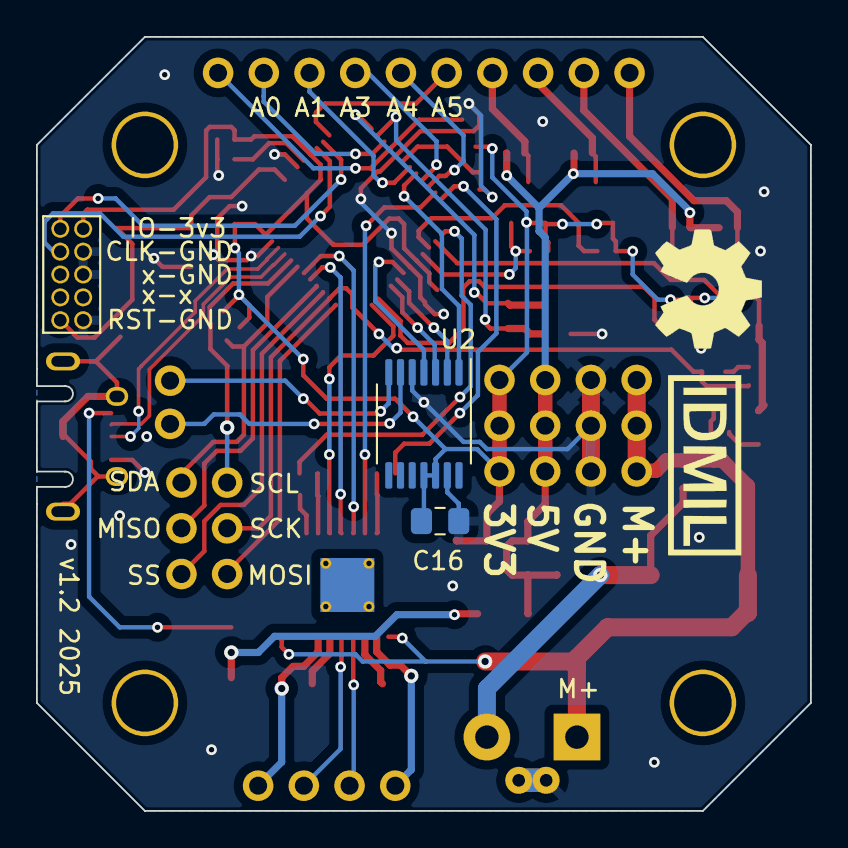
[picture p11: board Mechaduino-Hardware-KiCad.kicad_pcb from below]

Board: 2 copper layers, 43.0 x 43.0 mm, 62 parts (3 on the bottom side), 59 nets.

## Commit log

2026-03-13 Initial commit, hardware v1.2.
    [Mechaduino-Hardware-KiCad-B_Cu.gbl, Mechaduino-Hardware-KiCad-B_Mask.gbs, Mechaduino-Hardware-KiCad-B_Paste.gbp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]
2026-03-14 Updated README.md, added image, and removed unnecessary schematic files
    [io.kicad_sch, power.kicad_sch]
